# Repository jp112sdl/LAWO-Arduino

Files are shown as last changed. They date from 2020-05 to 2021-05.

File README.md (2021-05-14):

# LAWO-FlipDot
Arduino library for LAWO XY5 flipdot displays (also for GORBA and other FP2800 based flipdot displays)

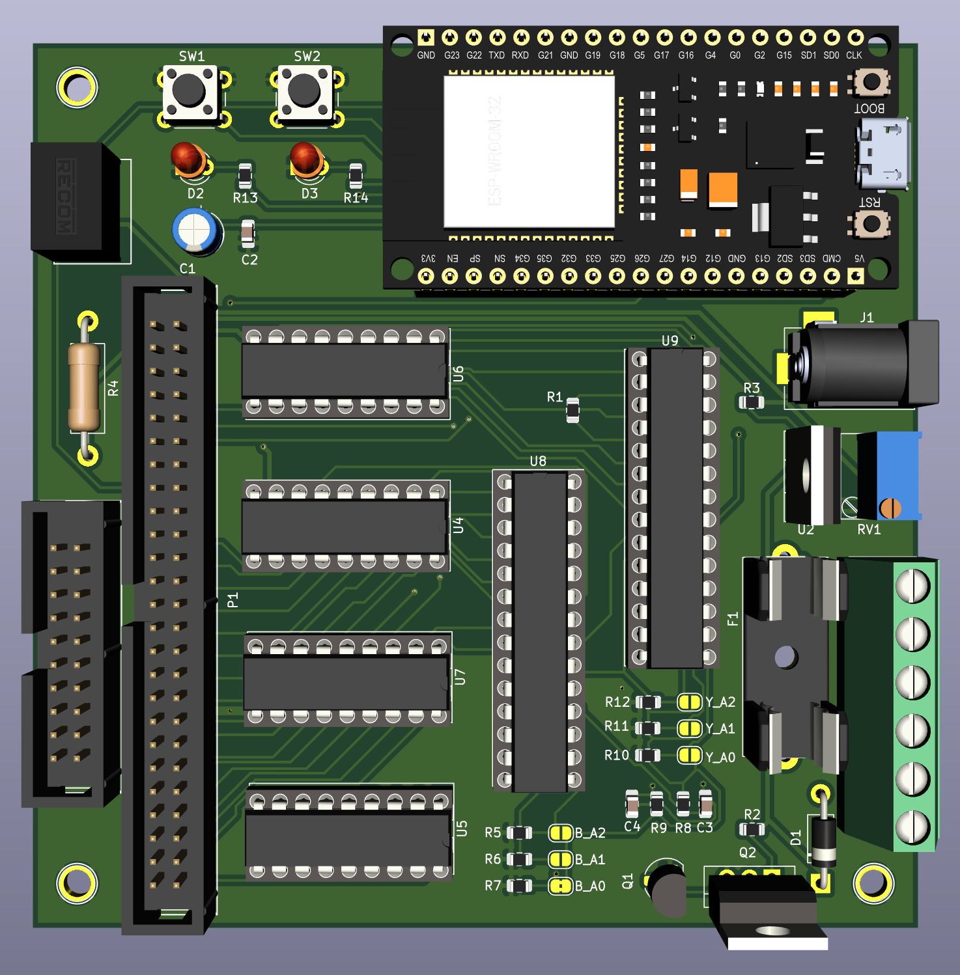
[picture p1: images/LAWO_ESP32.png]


### BOM (mostly from reichelt.de)

| Qty	| Reference(s)	| Value |	Order No. / URL	| Supplier
|---|---|---|---|---|
|1|	C1	|100u	|RAD 100/25|	reichelt
|3 |	C2, C3, C4|100n|	X7R-5 100N	|reichelt
|1|	F1	|T500mA	|RND 170-00041	|reichelt
|1|	F1	|Fuse Holder |RND 170-00188 |reichelt
|1|P1	|MATRIX	|WSL 50G	|reichelt
|1|P2	|MUX|	WSL 20G	|reichelt
|1|Q1	|BC547|	BC 547C	|reichelt
|1|Q2	|IRF740	|IRF 740	|reichelt
|1|	R4|	56|	2W METALL 56	|reichelt
|1|	RV1|	5k|	64W-5,0K|	reichelt
|1	|U1|LC78_05-0.5	|LC78_05-0.5	|reichelt
|1|	U2	|LM317T	|LM 317-220	|reichelt
|1| J1 | Barrel Jack | DC BU25 90|reichelt
|1| J2 | 1x6 Screw Terminal Block, 5mm | RND 205-00049 |reichelt
|1| D1| 1N4001 | 1N 4001|reichelt|
|1| D2| LED1 | LED 3MM GN |reichelt|
|1| D3| LED2 | LED 3MM RT|reichelt
|2| SW1, SW2| TASTER 9303 | reichelt
|4| U4,U5,U6,U7	|Sockel	|GS 18	|reichelt
|2|U8,U9	|Sockel	|GS 28-S	|reichelt
|2| U5,U4	|ULN2803A	|ULN 2803A|	reichelt
|2	|U6,U7	|UDN2981A	|UDN 2981	|reichelt
|2| U8, U9 | MCP23017 | MCP 23017-E/SP | reichelt
|2| R13, R14 | 330 SMD 0805 | RND 0805 1 330 | reichelt
|1| R3 | 240 SMD 0805 | RND 0805 1 240 | reichelt
|2| R17, R18 | 4k7 SMD 0805 | RND 0805 1 4,7K  | reichelt
|12| R1, R2, R5, R6, R7, R8, R9, R10, R11, R12, R15, R16 | 10k SMD 0805 | RND 0805 1 10K  | reichelt
| 1 | U3 | ESP32 Module | AZDelivery ESP32 NodeMCU Module | [amazon.de](https://www.amazon.de/AZDelivery-NodeMCU-Development-Nachfolgermodell-ESP8266/dp/B071P98VTG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)

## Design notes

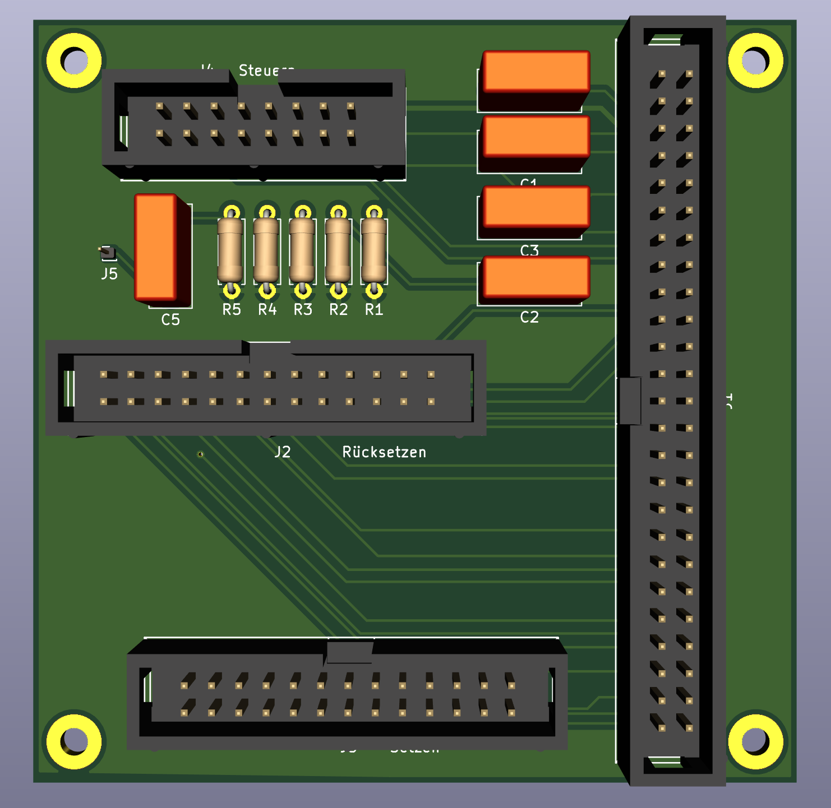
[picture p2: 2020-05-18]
images/GORBA_LAWO_Adapter.png

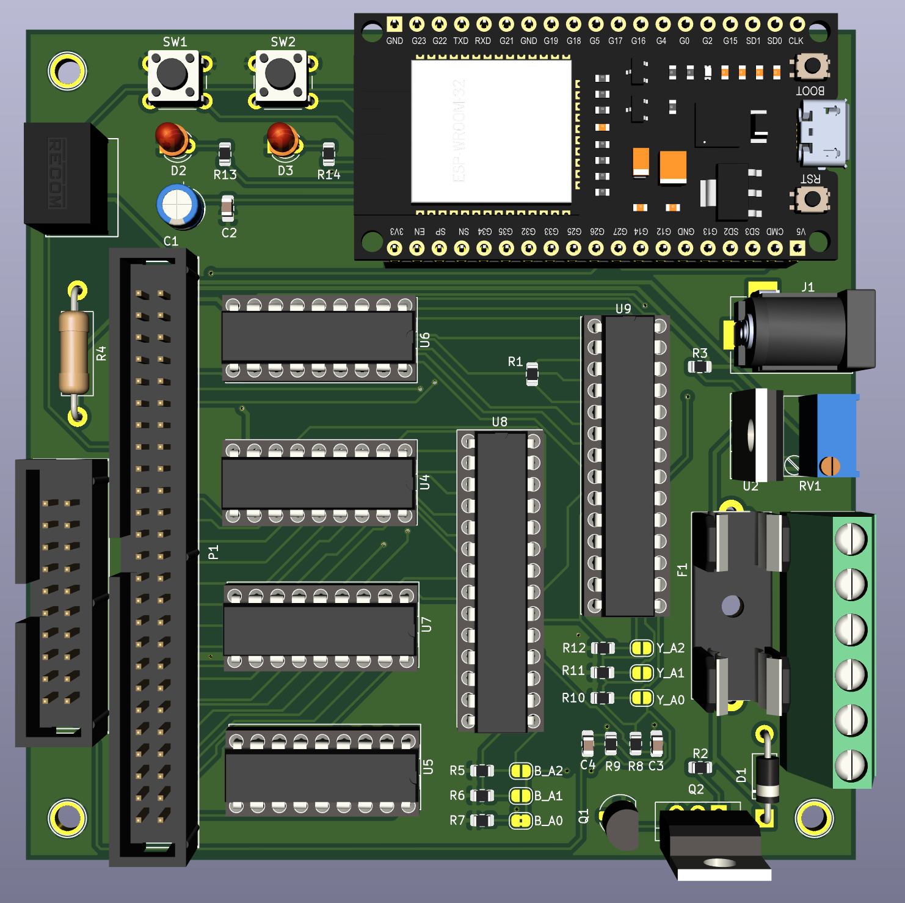
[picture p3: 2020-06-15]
PCB/LAWO_ESP32/LAWO_ESP32.png

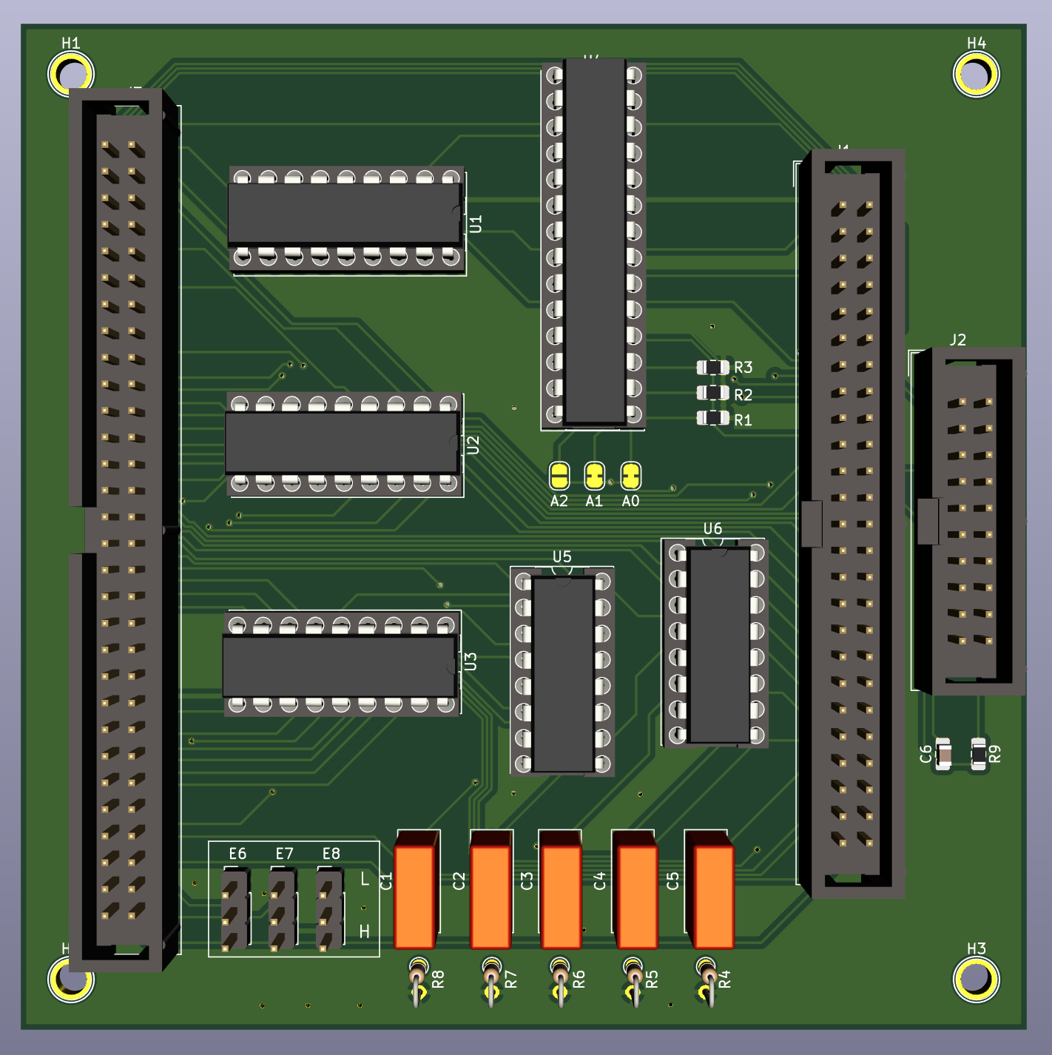
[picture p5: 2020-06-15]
PCB/BROSE_LAWO_Adapter/BROSE_LAWO_Adapter.dsn.png

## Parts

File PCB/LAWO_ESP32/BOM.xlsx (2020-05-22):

Reference | Value | Footprint | Datasheet | Feld4
C1 | 100n | Capacitor_SMD:C_0805_2012Metric_Pad1.15x1.40mm_HandSolder
C2 | 100u | Capacitors_THT:CP_Radial_D5.0mm_P2.00mm
C3 | 100n | Capacitor_SMD:C_0805_2012Metric_Pad1.15x1.40mm_HandSolder | ~
C4 | 100n | Capacitor_SMD:C_0805_2012Metric_Pad1.15x1.40mm_HandSolder | ~
D1 | 1N4001 | Diode_THT:D_DO-41_SOD81_P10.16mm_Horizontal
D2 | LED1 | LED_THT:LED_D3.0mm | ~
D3 | LED2 | LED_THT:LED_D3.0mm | ~
F1 | T500mA | Fuse_Holders_and_Fuses:Fuseholder5x20_horiz_open_Schurter_0031_8201
J1 | Barrel_Jack | Connectors:BARREL_JACK | ~
J2 | Screw_Terminal_01x06 | Connectors_Terminal_Blocks:TerminalBlock_bornier-6_P5.08mm | ~
P1 | MATRIX | Connect:IDC_Header_Straight_50pins
P2 | MUX | Connect:IDC_Header_Straight_20pins
Q1 | BC547 | Package_TO_SOT_THT:TO-92_HandSolder | http://www.fairchildsemi.com/ds/BC/BC547.pdf
Q2 | IRF740 | Package_TO_SOT_THT:TO-220-3_Vertical | http://www.vishay.com/docs/91054/91054.pdf
R1 | 10k | Resistor_SMD:R_0805_2012Metric
R10 | 10k | Resistor_SMD:R_0805_2012Metric | ~
R11 | 10k | Resistor_SMD:R_0805_2012Metric | ~
R12 | 10k | Resistor_SMD:R_0805_2012Metric | ~
R13 | 330 | Resistor_SMD:R_0805_2012Metric | ~
R14 | 330 | Resistor_SMD:R_0805_2012Metric | ~
R15 | 10k | Resistor_SMD:R_0805_2012Metric
R16 | 10k | Resistor_SMD:R_0805_2012Metric
R17 | 4,7k | Resistor_SMD:R_0805_2012Metric | ~
R18 | 4,7k | Resistor_SMD:R_0805_2012Metric | ~
R2 | 10k | Resistor_SMD:R_0805_2012Metric
R3 | 240 | Resistor_SMD:R_0805_2012Metric
R4 | 56 | Resistor_THT:R_Axial_DIN0411_L9.9mm_D3.6mm_P15.24mm_Horizontal
R5 | 10k | Resistor_SMD:R_0805_2012Metric | ~
R6 | 10k | Resistor_SMD:R_0805_2012Metric | ~
R7 | 10k | Resistor_SMD:R_0805_2012Metric | ~
R8 | 10k | Resistor_SMD:R_0805_2012Metric | ~
R9 | 10k | Resistor_SMD:R_0805_2012Metric | ~
RV1 | 5k | Potentiometers:Potentiometer_Trimmer_Bourns_3299W
SW1 | T1 | Buttons_Switches_THT:SW_PUSH_6mm_h5mm | ~
SW2 | T2 | Buttons_Switches_THT:SW_PUSH_6mm_h5mm | ~
U1 | LC78_05-0.5 | Package_SIP:SIP3_11.6x8.5mm | http://www.st.com/content/ccc/resource/technical/document/datasheet/41/4f/b3/b0/12/d4/47/88/CD00000444.pdf/files/CD00000444.pdf/jcr:content/translations/en.CD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
U2 | LM317T | TO_SOT_Packages_THT:TO-220-3_Vertical
U3 | ESP32-DEVKITC-32D | additional:MODULE_ESP32-DEVKITC-32D | Espressif Systems | 4
U4 | ULN2803A | Package_DIP:DIP-18_W7.62mm_Socket
U5 | ULN2803A | Package_DIP:DIP-18_W7.62mm_Socket
U6 | UDN2981A / TBD62783AFG | Package_DIP:DIP-18_W7.62mm_Socket
U7 | UDN2981A / TBD62783AFG | Package_DIP:DIP-18_W7.62mm_Socket
U8 | MCP23017 | Package_DIP:DIP-28_W7.62mm_Socket | http://ww1.microchip.com/downloads/en/DeviceDoc/20001952C.pdf
U9 | MCP23017 | Package_DIP:DIP-28_W7.62mm_Socket | http://ww1.microchip.com/downloads/en/DeviceDoc/20001952C.pdf

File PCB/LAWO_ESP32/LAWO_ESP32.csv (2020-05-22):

Reference | Value | Footprint | Datasheet | Feld4
F1 | T500mA | Fuse_Holders_and_Fuses:Fuseholder5x20_horiz_open_Schurter_0031_8201
R5 | 10k | Resistor_SMD:R_0805_2012Metric | ~
R6 | 10k | Resistor_SMD:R_0805_2012Metric | ~
R1 | 10k | Resistor_SMD:R_0805_2012Metric
R7 | 10k | Resistor_SMD:R_0805_2012Metric | ~
R2 | 10k | Resistor_SMD:R_0805_2012Metric
R8 | 10k | Resistor_SMD:R_0805_2012Metric | ~
R3 | 240 | Resistor_SMD:R_0805_2012Metric
R4 | 56 | Resistor_THT:R_Axial_DIN0411_L9.9mm_D3.6mm_P15.24mm_Horizontal
R9 | 10k | Resistor_SMD:R_0805_2012Metric | ~
R10 | 10k | Resistor_SMD:R_0805_2012Metric | ~
R11 | 10k | Resistor_SMD:R_0805_2012Metric | ~
R12 | 10k | Resistor_SMD:R_0805_2012Metric | ~
JP1 | B_A2 | Jumper:SolderJumper-2_P1.3mm_Open_RoundedPad1.0x1.5mm | ~
JP2 | B_A1 | Jumper:SolderJumper-2_P1.3mm_Open_RoundedPad1.0x1.5mm | ~
JP3 | B_A0 | Jumper:SolderJumper-2_P1.3mm_Bridged2Bar_RoundedPad1.0x1.5mm | ~
JP4 | Y_A0 | Jumper:SolderJumper-2_P1.3mm_Open_RoundedPad1.0x1.5mm | ~
JP5 | Y_A1 | Jumper:SolderJumper-2_P1.3mm_Open_RoundedPad1.0x1.5mm | ~
JP6 | Y_A2 | Jumper:SolderJumper-2_P1.3mm_Open_RoundedPad1.0x1.5mm | ~
D1 | 1N4001 | Diode_THT:D_DO-41_SOD81_P10.16mm_Horizontal
MH1 | MountingHole | Connect:1pin
MH2 | MountingHole | Connect:1pin
MH3 | MountingHole | Connect:1pin
MH4 | MountingHole | Connect:1pin
C3 | 100n | Capacitor_SMD:C_0805_2012Metric_Pad1.15x1.40mm_HandSolder | ~
C2 | 100u | Capacitors_THT:CP_Radial_D5.0mm_P2.00mm
C1 | 100n | Capacitor_SMD:C_0805_2012Metric_Pad1.15x1.40mm_HandSolder
C4 | 100n | Capacitor_SMD:C_0805_2012Metric_Pad1.15x1.40mm_HandSolder | ~
RV1 | 5k | Potentiometers:Potentiometer_Trimmer_Bourns_3299W
J1 | Barrel_Jack | Connectors:BARREL_JACK | ~
U1 | L7805 | Package_SIP:SIP3_11.6x8.5mm | http://www.st.com/content/ccc/resource/technical/document/datasheet/41/4f/b3/b0/12/d4/47/88/CD00000444.pdf/files/CD00000444.pdf/jcr:content/translations/en.CD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
U2 | LM317T | TO_SOT_Packages_THT:TO-220-3_Vertical
P2 | MUX | Connect:IDC_Header_Straight_20pins
P1 | MATRIX | Connect:IDC_Header_Straight_50pins
U4 | ULN2803A | Package_DIP:DIP-18_W7.62mm_Socket
U5 | ULN2803A | Package_DIP:DIP-18_W7.62mm_Socket
U6 | UDN2981A / TBD62783AFG | Package_DIP:DIP-18_W7.62mm_Socket
U8 | MCP23017 | Package_DIP:DIP-28_W7.62mm_Socket | http://ww1.microchip.com/downloads/en/DeviceDoc/20001952C.pdf
U9 | MCP23017 | Package_DIP:DIP-28_W7.62mm_Socket | http://ww1.microchip.com/downloads/en/DeviceDoc/20001952C.pdf
U3 | ESP32-DEVKITC-32D | additional:MODULE_ESP32-DEVKITC-32D | Espressif Systems | 4
J2 | Screw_Terminal_01x06 | Connectors_Terminal_Blocks:TerminalBlock_bornier-6_P5.08mm | ~
U7 | UDN2981A / TBD62783AFG | Package_DIP:DIP-18_W7.62mm_Socket
Q2 | IRF740 | Package_TO_SOT_THT:TO-220-3_Vertical | http://www.vishay.com/docs/91054/91054.pdf
Q1 | BC547 | Package_TO_SOT_THT:TO-92_HandSolder | http://www.fairchildsemi.com/ds/BC/BC547.pdf
SW1 | T1 | Buttons_Switches_THT:SW_PUSH_6mm_h5mm | ~
SW2 | T2 | Buttons_Switches_THT:SW_PUSH_6mm_h5mm | ~
R13 | 330 | Resistor_SMD:R_0805_2012Metric | ~
D2 | LED1 | LED_THT:LED_D3.0mm | ~
R14 | 330 | Resistor_SMD:R_0805_2012Metric | ~
D3 | LED2 | LED_THT:LED_D3.0mm | ~
R15 | 10k | Resistor_SMD:R_0805_2012Metric
R16 | 10k | Resistor_SMD:R_0805_2012Metric
R17 | 4,7k | Resistor_SMD:R_0805_2012Metric | ~
R18 | 4,7k | Resistor_SMD:R_0805_2012Metric | ~

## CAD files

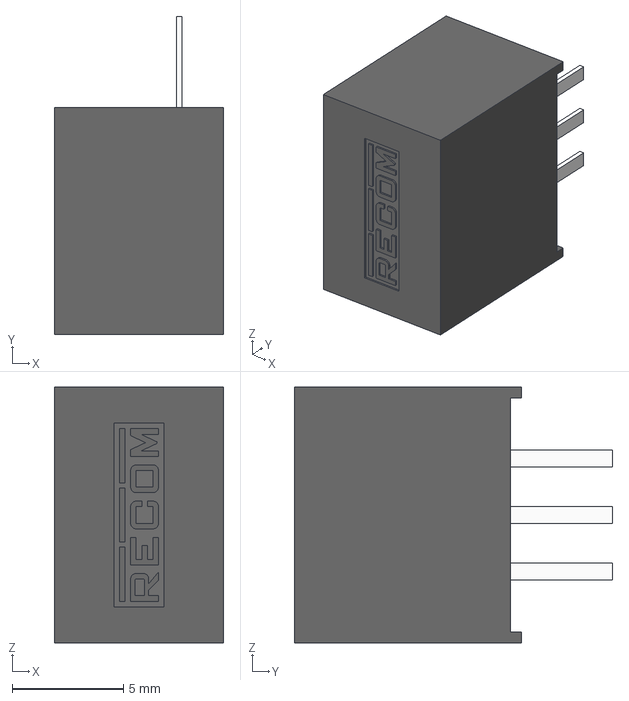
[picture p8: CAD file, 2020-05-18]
PCB/LAWO_ESP32/additional/R-782.5-0.5--3DModel-STEP-1.STEP
7.60 x 14.3 x 11.5 mm

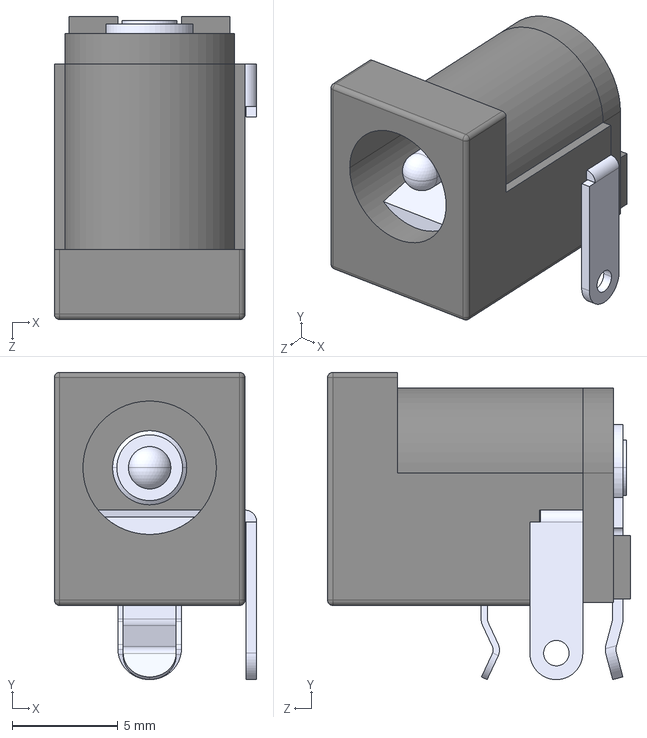
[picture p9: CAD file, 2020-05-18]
PCB/LAWO_ESP32/additional/DCJ200-10-A-K1-K--3DModel-STEP-56544.STEP
9.55 x 14.5 x 14.3 mm

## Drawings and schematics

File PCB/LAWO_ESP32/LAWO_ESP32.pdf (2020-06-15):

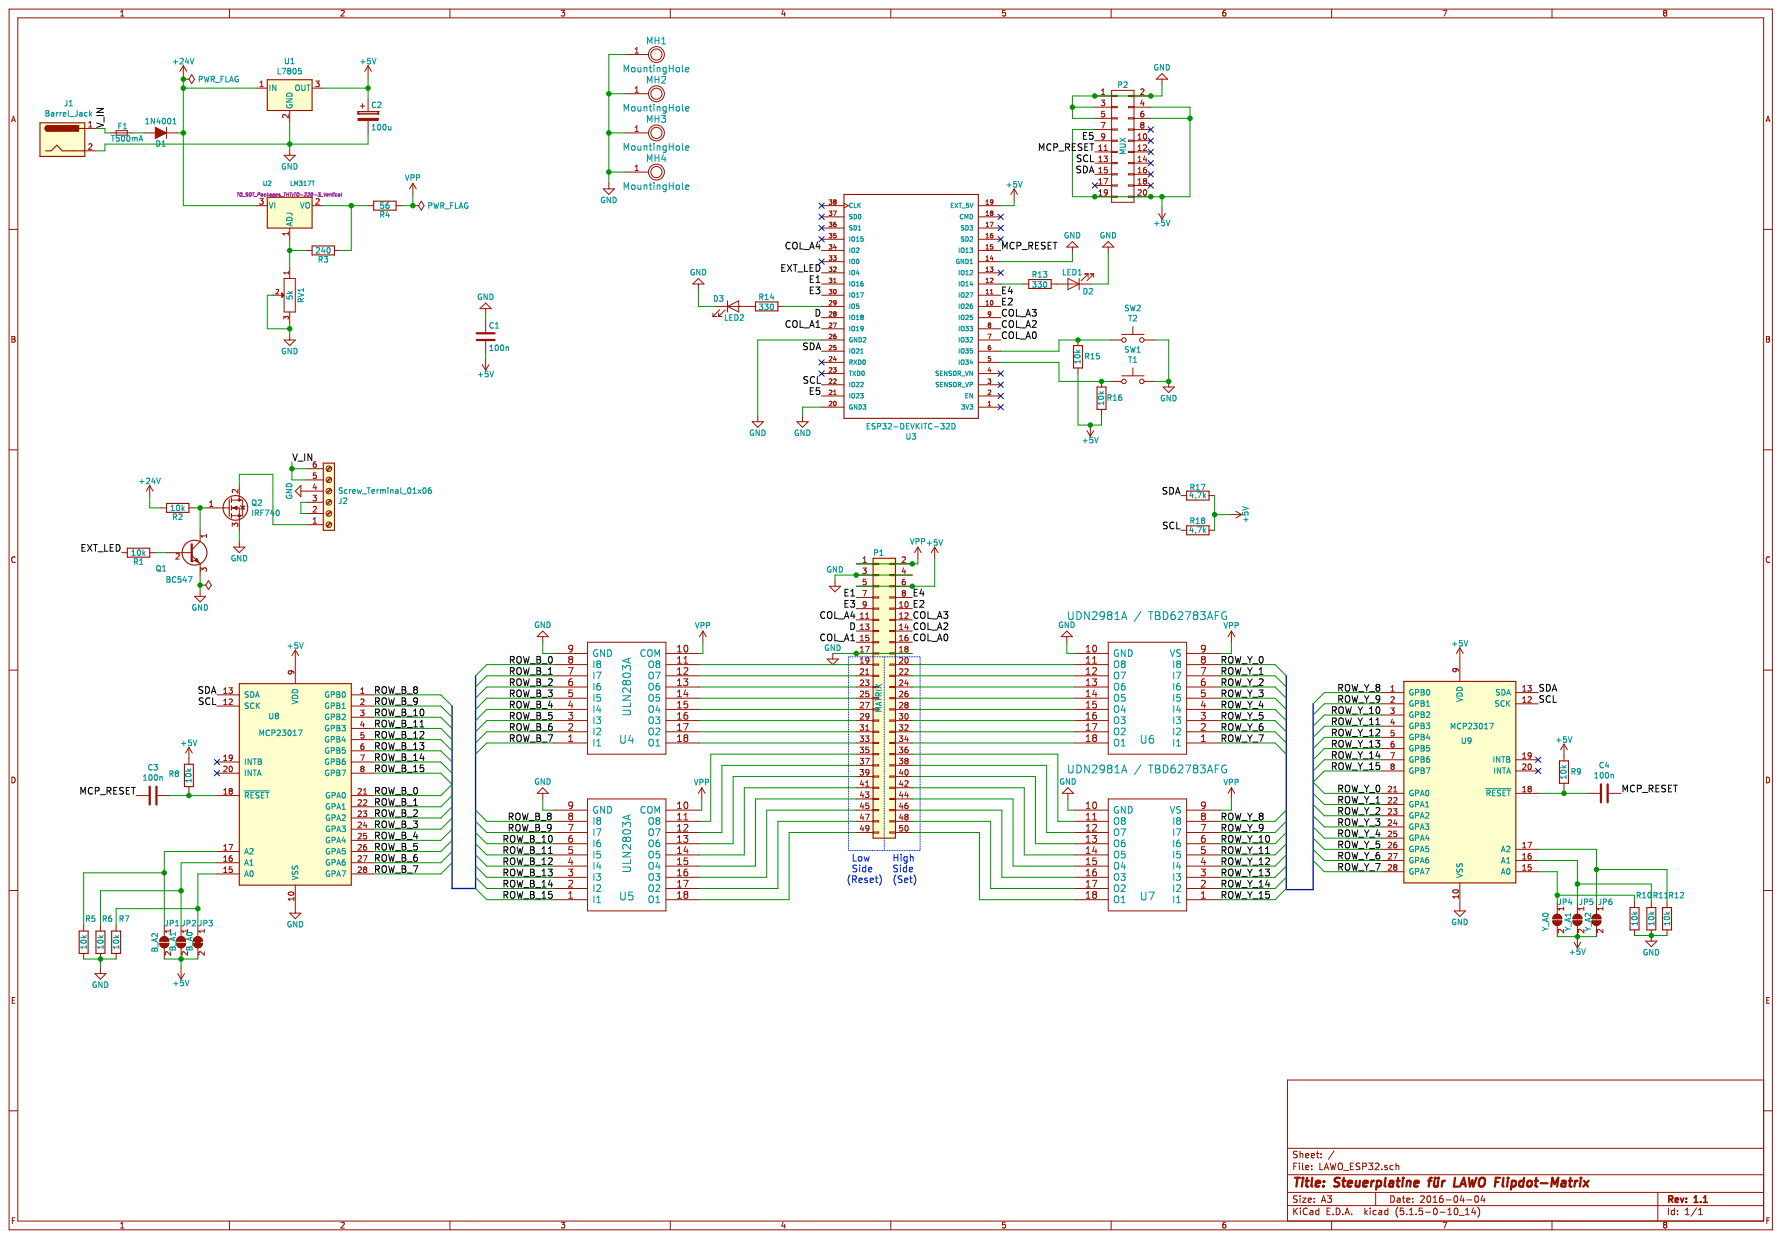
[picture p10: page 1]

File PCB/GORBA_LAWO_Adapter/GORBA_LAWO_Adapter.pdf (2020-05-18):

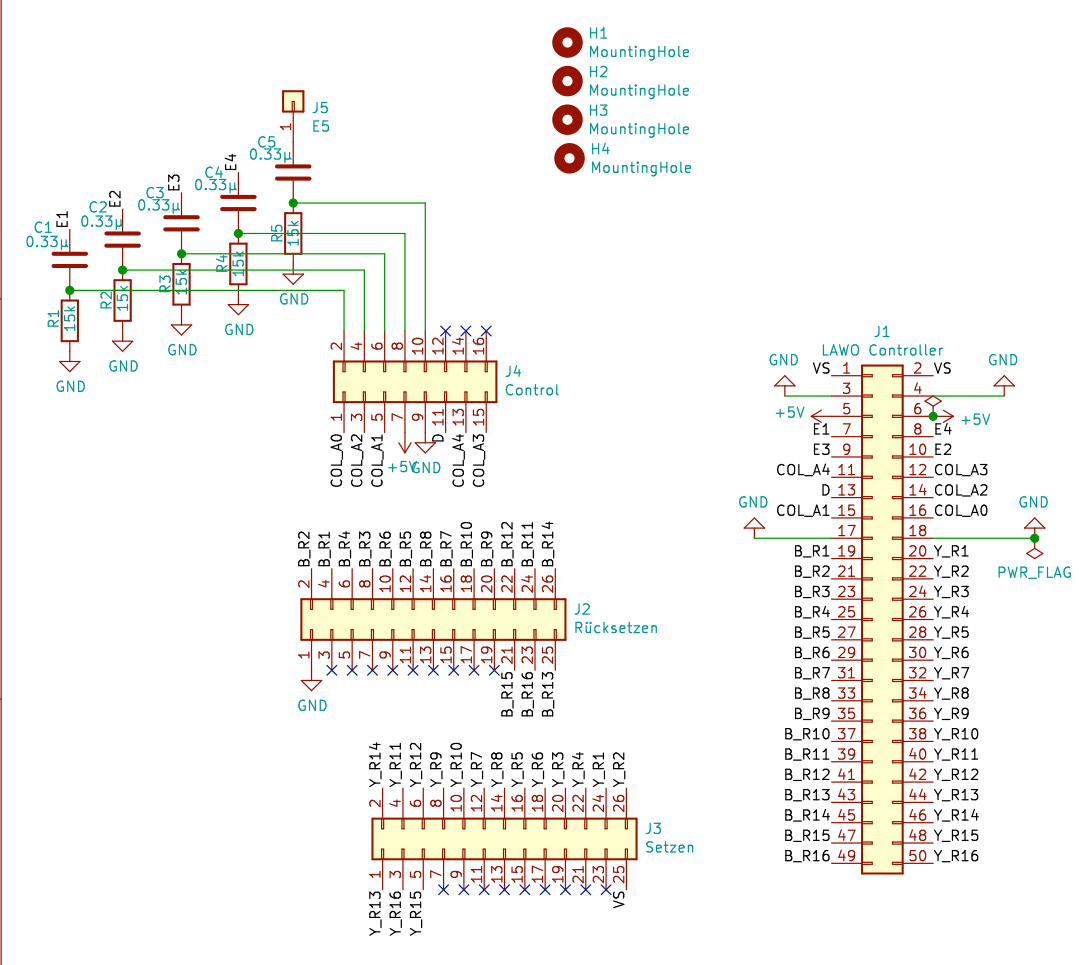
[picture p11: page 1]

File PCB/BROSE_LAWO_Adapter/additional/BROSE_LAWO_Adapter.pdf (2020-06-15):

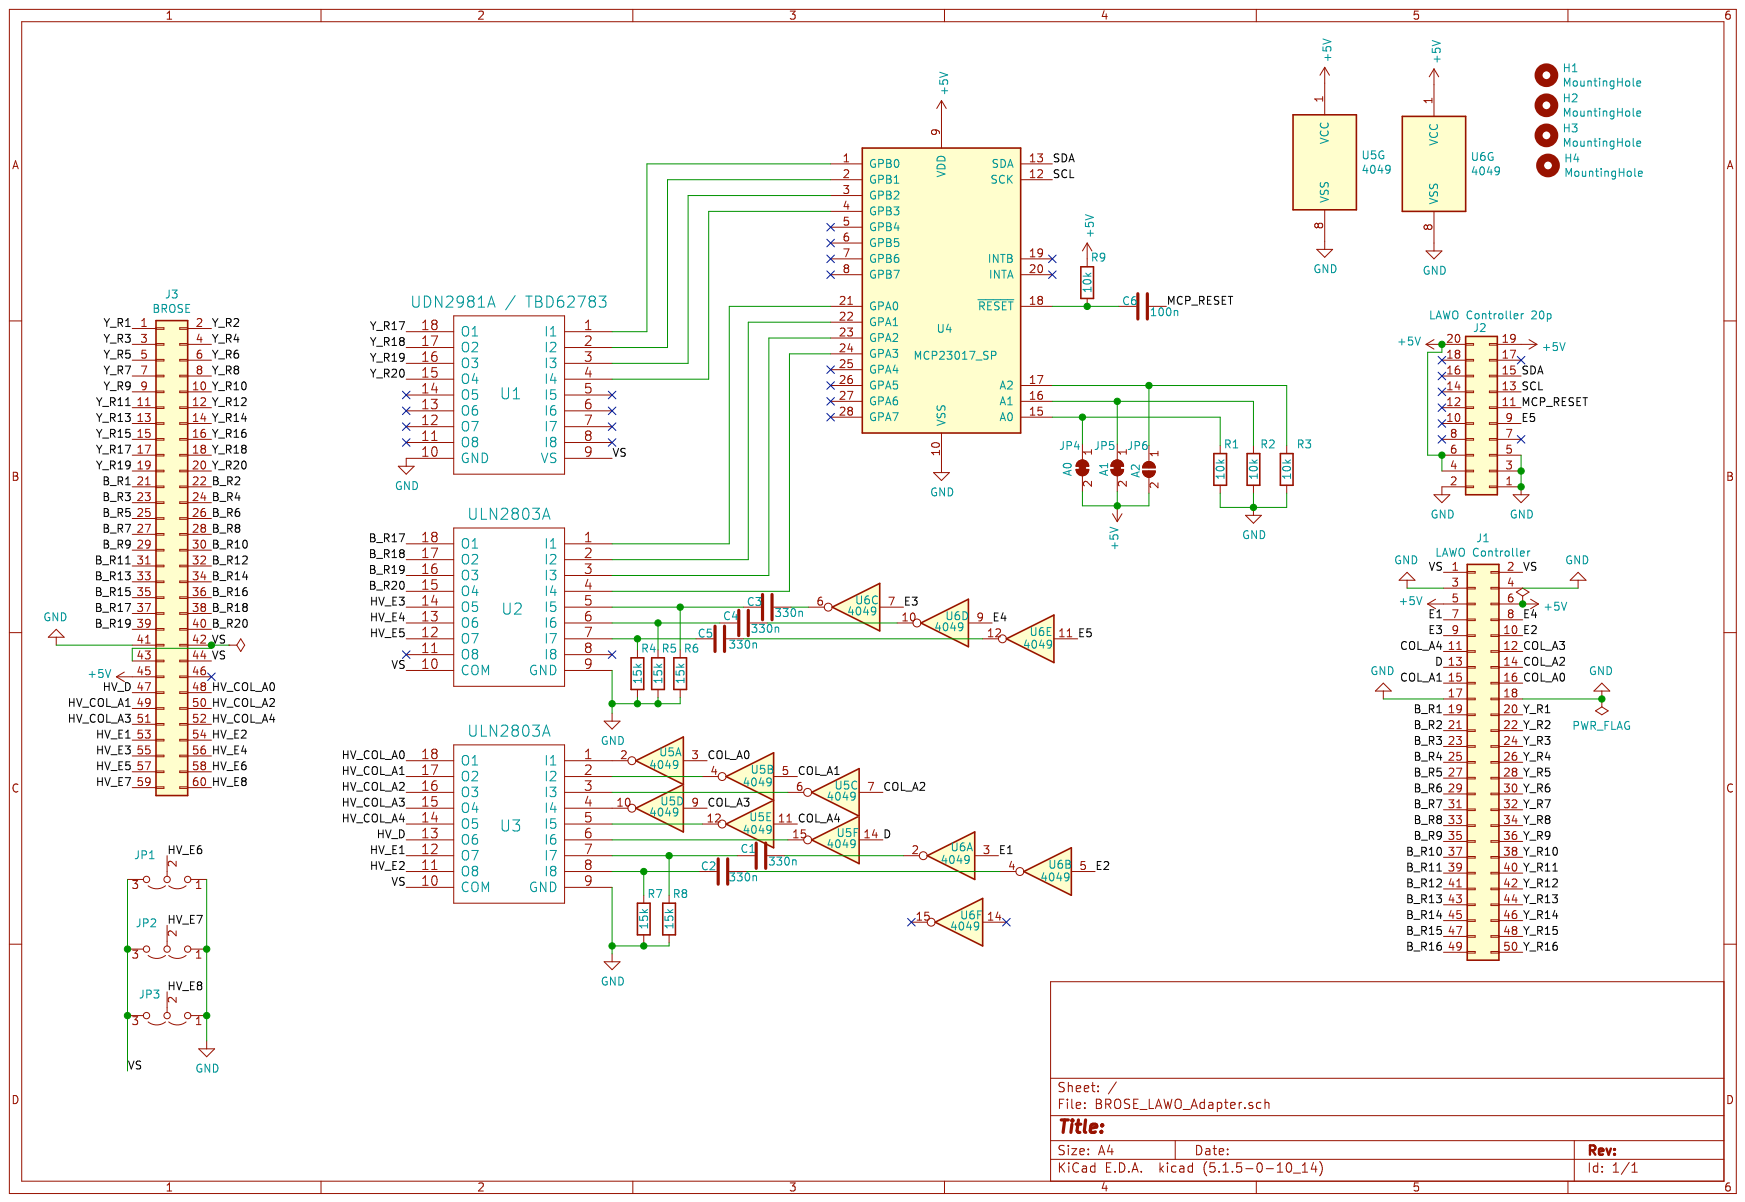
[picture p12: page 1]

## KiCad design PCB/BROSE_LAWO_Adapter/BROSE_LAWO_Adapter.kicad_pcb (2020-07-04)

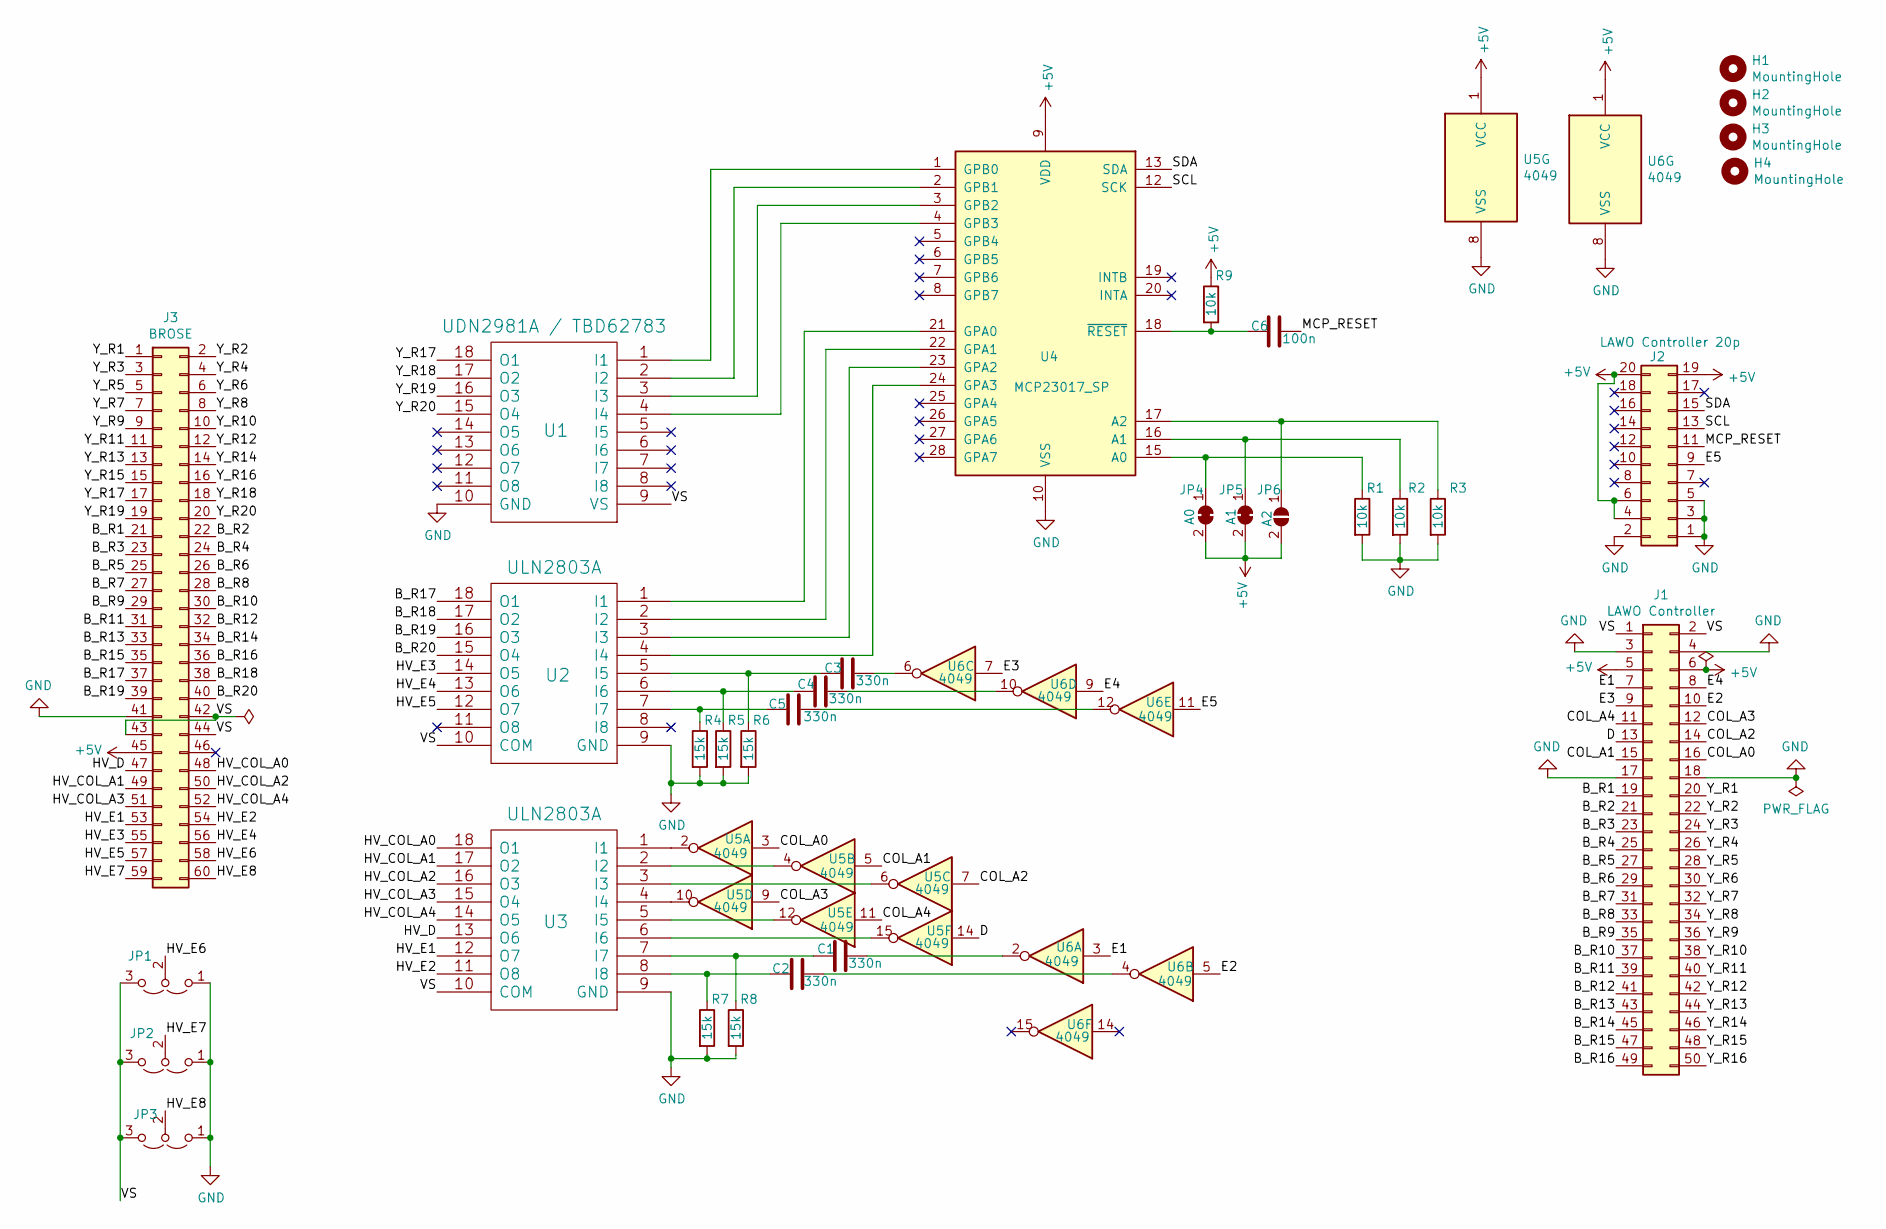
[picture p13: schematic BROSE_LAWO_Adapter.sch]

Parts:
C1, C2, C3, C4, C5: 330n; C_Rect_L10.0mm_W4.0mm_P7.50mm_MKS4
C6: 100n; C_0805_2012Metric_Pad1.15x1.40mm_HandSolder
H1, H2, H3, H4: MountingHole; 1pin
J1: LAWO Controller; IDC-Header_2x25_P2.54mm_Vertical
J2: LAWO Controller 20p; IDC-Header_2x10_P2.54mm_Vertical
J3: BROSE; IDC-Header_2x30_P2.54mm_Vertical
JP1: E6; PinHeader_1x03_P2.54mm_Vertical
JP2: E7; PinHeader_1x03_P2.54mm_Vertical
JP3: E8; PinHeader_1x03_P2.54mm_Vertical
JP4: A0; SolderJumper-2_P1.3mm_Bridged_RoundedPad1.0x1.5mm
JP5: A1; SolderJumper-2_P1.3mm_Bridged_RoundedPad1.0x1.5mm
JP6: A2; SolderJumper-2_P1.3mm_Open_RoundedPad1.0x1.5mm
R1, R2, R3, R9: 10k; R_0805_2012Metric_Pad1.15x1.40mm_HandSolder
R4, R5, R6, R7, R8: 15k; R_Axial_DIN0204_L3.6mm_D1.6mm_P2.54mm_Vertical
U1: UDN2981A / TBD62783; DIP-18_W7.62mm_Socket
U2, U3: ULN2803A; DIP-18_W7.62mm_Socket
U4: MCP23017_SP; DIP-28_W7.62mm_Socket
U5, U6: 4049; DIP-16_W7.62mm_Socket

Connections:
+5V: J1.5, J1.6, J2.4, J2.6, J2.19, J2.20, J3.45, JP4.2 (B), JP5.2 (B), JP6.2 (B), R9.1, U4.9 (VDD), U5.1 (VCC), U6.1 (VCC)
/B_R1: J1.19, J3.21
/B_R2: J1.21, J3.22
/B_R3: J1.23, J3.23
/B_R4: J1.25, J3.24
/B_R5: J1.27, J3.25
/B_R6: J1.29, J3.26
/B_R7: J1.31, J3.27
/B_R8: J1.33, J3.28
/B_R9: J1.35, J3.29
/B_R10: J1.37, J3.30
/B_R11: J1.39, J3.31
/B_R12: J1.41, J3.32
/B_R13: J1.43, J3.33
/B_R14: J1.45, J3.34
/B_R15: J1.47, J3.35
/B_R16: J1.49, J3.36
/B_R17: J3.37, U2.18 (O1)
/B_R18: J3.38, U2.17 (O2)
/B_R19: J3.39, U2.16 (O3)
/B_R20: J3.40, U2.15 (O4)
/COL_A0: J1.16, U5.3
/COL_A1: J1.15, U5.5
/COL_A2: J1.14, U5.7
/COL_A3: J1.12, U5.9
/COL_A4: J1.11, U5.11
/D: J1.13, U5.14
/E1: J1.7, U6.3
/E2: J1.10, U6.5
/E3: J1.9, U6.7
/E4: J1.8, U6.9
/E5: J2.9, U6.11
/HV_COL_A0: J3.48, U3.18 (O1)
/HV_COL_A1: J3.49, U3.17 (O2)
/HV_COL_A2: J3.50, U3.16 (O3)
/HV_COL_A3: J3.51, U3.15 (O4)
/HV_COL_A4: J3.52, U3.14 (O5)
/HV_D: J3.47, U3.13 (O6)
/HV_E1: J3.53, U3.12 (O7)
/HV_E2: J3.54, U3.11 (O8)
/HV_E3: J3.55, U2.14 (O5)
/HV_E4: J3.56, U2.13 (O6)
/HV_E5: J3.57, U2.12 (O7)
/HV_E6: J3.58, JP1.2 (C)
/HV_E7: J3.59, JP2.2 (C)
/HV_E8: J3.60, JP3.2 (C)
/MCP_RESET: C6.2, J2.11
/SCL: J2.13, U4.12 (SCK)
/SDA: J2.15, U4.13 (SDA)
/VS: J1.1, J1.2, J3.42, J3.43, J3.44, JP1.3 (B), JP2.3 (B), JP3.3 (B), U1.9 (VS), U2.10 (COM), U3.10 (COM)
/Y_R1: J1.20, J3.1
/Y_R2: J1.22, J3.2
/Y_R3: J1.24, J3.3
/Y_R4: J1.26, J3.4
/Y_R5: J1.28, J3.5
/Y_R6: J1.30, J3.6
/Y_R7: J1.32, J3.7
/Y_R8: J1.34, J3.8
/Y_R9: J1.36, J3.9
/Y_R10: J1.38, J3.10
/Y_R11: J1.40, J3.11
/Y_R12: J1.42, J3.12
/Y_R13: J1.44, J3.13
/Y_R14: J1.46, J3.14
/Y_R15: J1.48, J3.15
/Y_R16: J1.50, J3.16
/Y_R17: J3.17, U1.18 (O1)
/Y_R18: J3.18, U1.17 (O2)
/Y_R19: J3.19, U1.16 (O3)
/Y_R20: J3.20, U1.15 (O4)
GND: J1.3, J1.4, J1.17, J1.18, J2.1, J2.2, J2.3, J2.5, J3.41, JP1.1 (A), JP2.1 (A), JP3.1 (A), R1.2, R2.2, R3.2, R4.2, R5.2, R6.2, R7.2, R8.2, U1.10 (GND), U2.9 (GND), U3.9 (GND), U4.10 (VSS), U5.8 (VSS), U6.8 (VSS)
unnamed: C1.1, R8.1, U3.7 (I7)
unnamed: C1.2, U6.2
unnamed: C2.1, R7.1, U3.8 (I8)
unnamed: C2.2, U6.4
unnamed: C3.1, R6.1, U2.5 (I5)
unnamed: C3.2, U6.6
unnamed: C4.1, R5.1, U2.6 (I6)
unnamed: C4.2, U6.10
unnamed: C5.1, R4.1, U2.7 (I7)
unnamed: C5.2, U6.12
unnamed: C6.1, R9.2, U4.18 (~RESET~)
unnamed: JP4.1 (A), R1.1, U4.15 (A0)
unnamed: JP5.1 (A), R2.1, U4.16 (A1)
unnamed: JP6.1 (A), R3.1, U4.17 (A2)
unnamed: U1.1 (I1), U4.1 (GPB0)
unnamed: U1.2 (I2), U4.2 (GPB1)
unnamed: U1.3 (I3), U4.3 (GPB2)
unnamed: U1.4 (I4), U4.4 (GPB3)
unnamed: U2.1 (I1), U4.21 (GPA0)
unnamed: U2.2 (I2), U4.22 (GPA1)
unnamed: U2.3 (I3), U4.23 (GPA2)
unnamed: U2.4 (I4), U4.24 (GPA3)
unnamed: U3.1 (I1), U5.2
unnamed: U3.2 (I2), U5.4
unnamed: U3.3 (I3), U5.6
unnamed: U3.4 (I4), U5.10
unnamed: U3.5 (I5), U5.12
unnamed: U3.6 (I6), U5.15

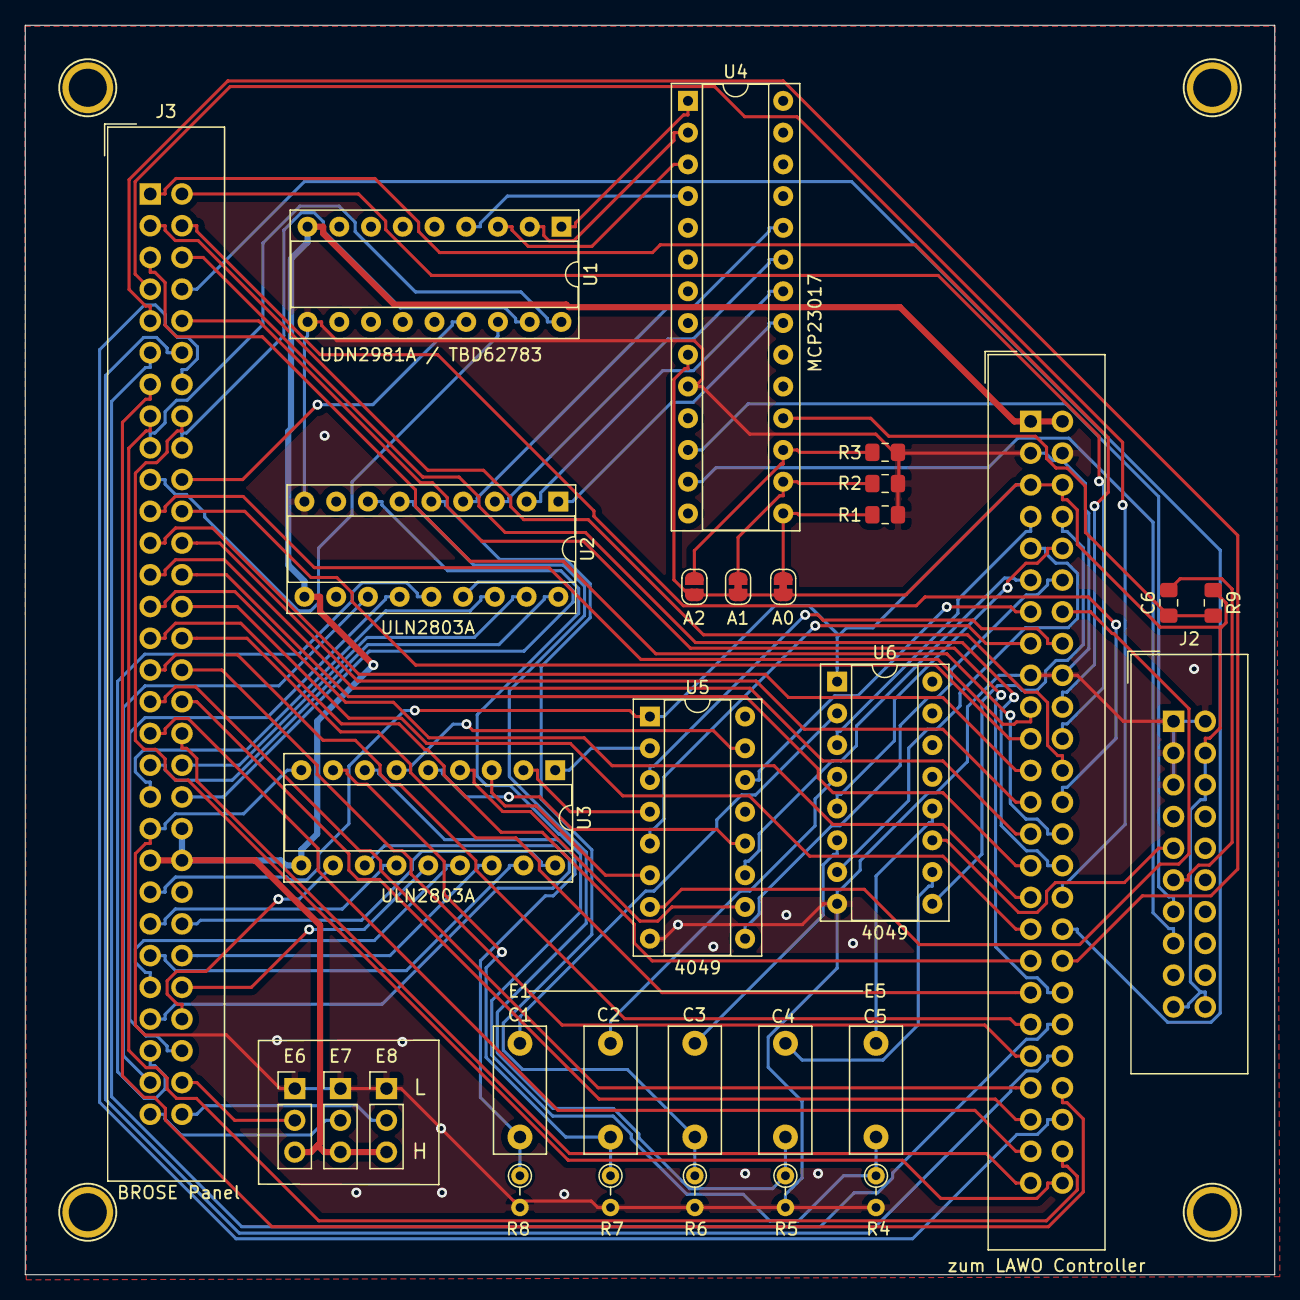
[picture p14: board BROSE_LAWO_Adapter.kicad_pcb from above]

Board: 2 copper layers, 100.0 x 100.0 mm, 34 parts (0 on the bottom side), 99 nets.

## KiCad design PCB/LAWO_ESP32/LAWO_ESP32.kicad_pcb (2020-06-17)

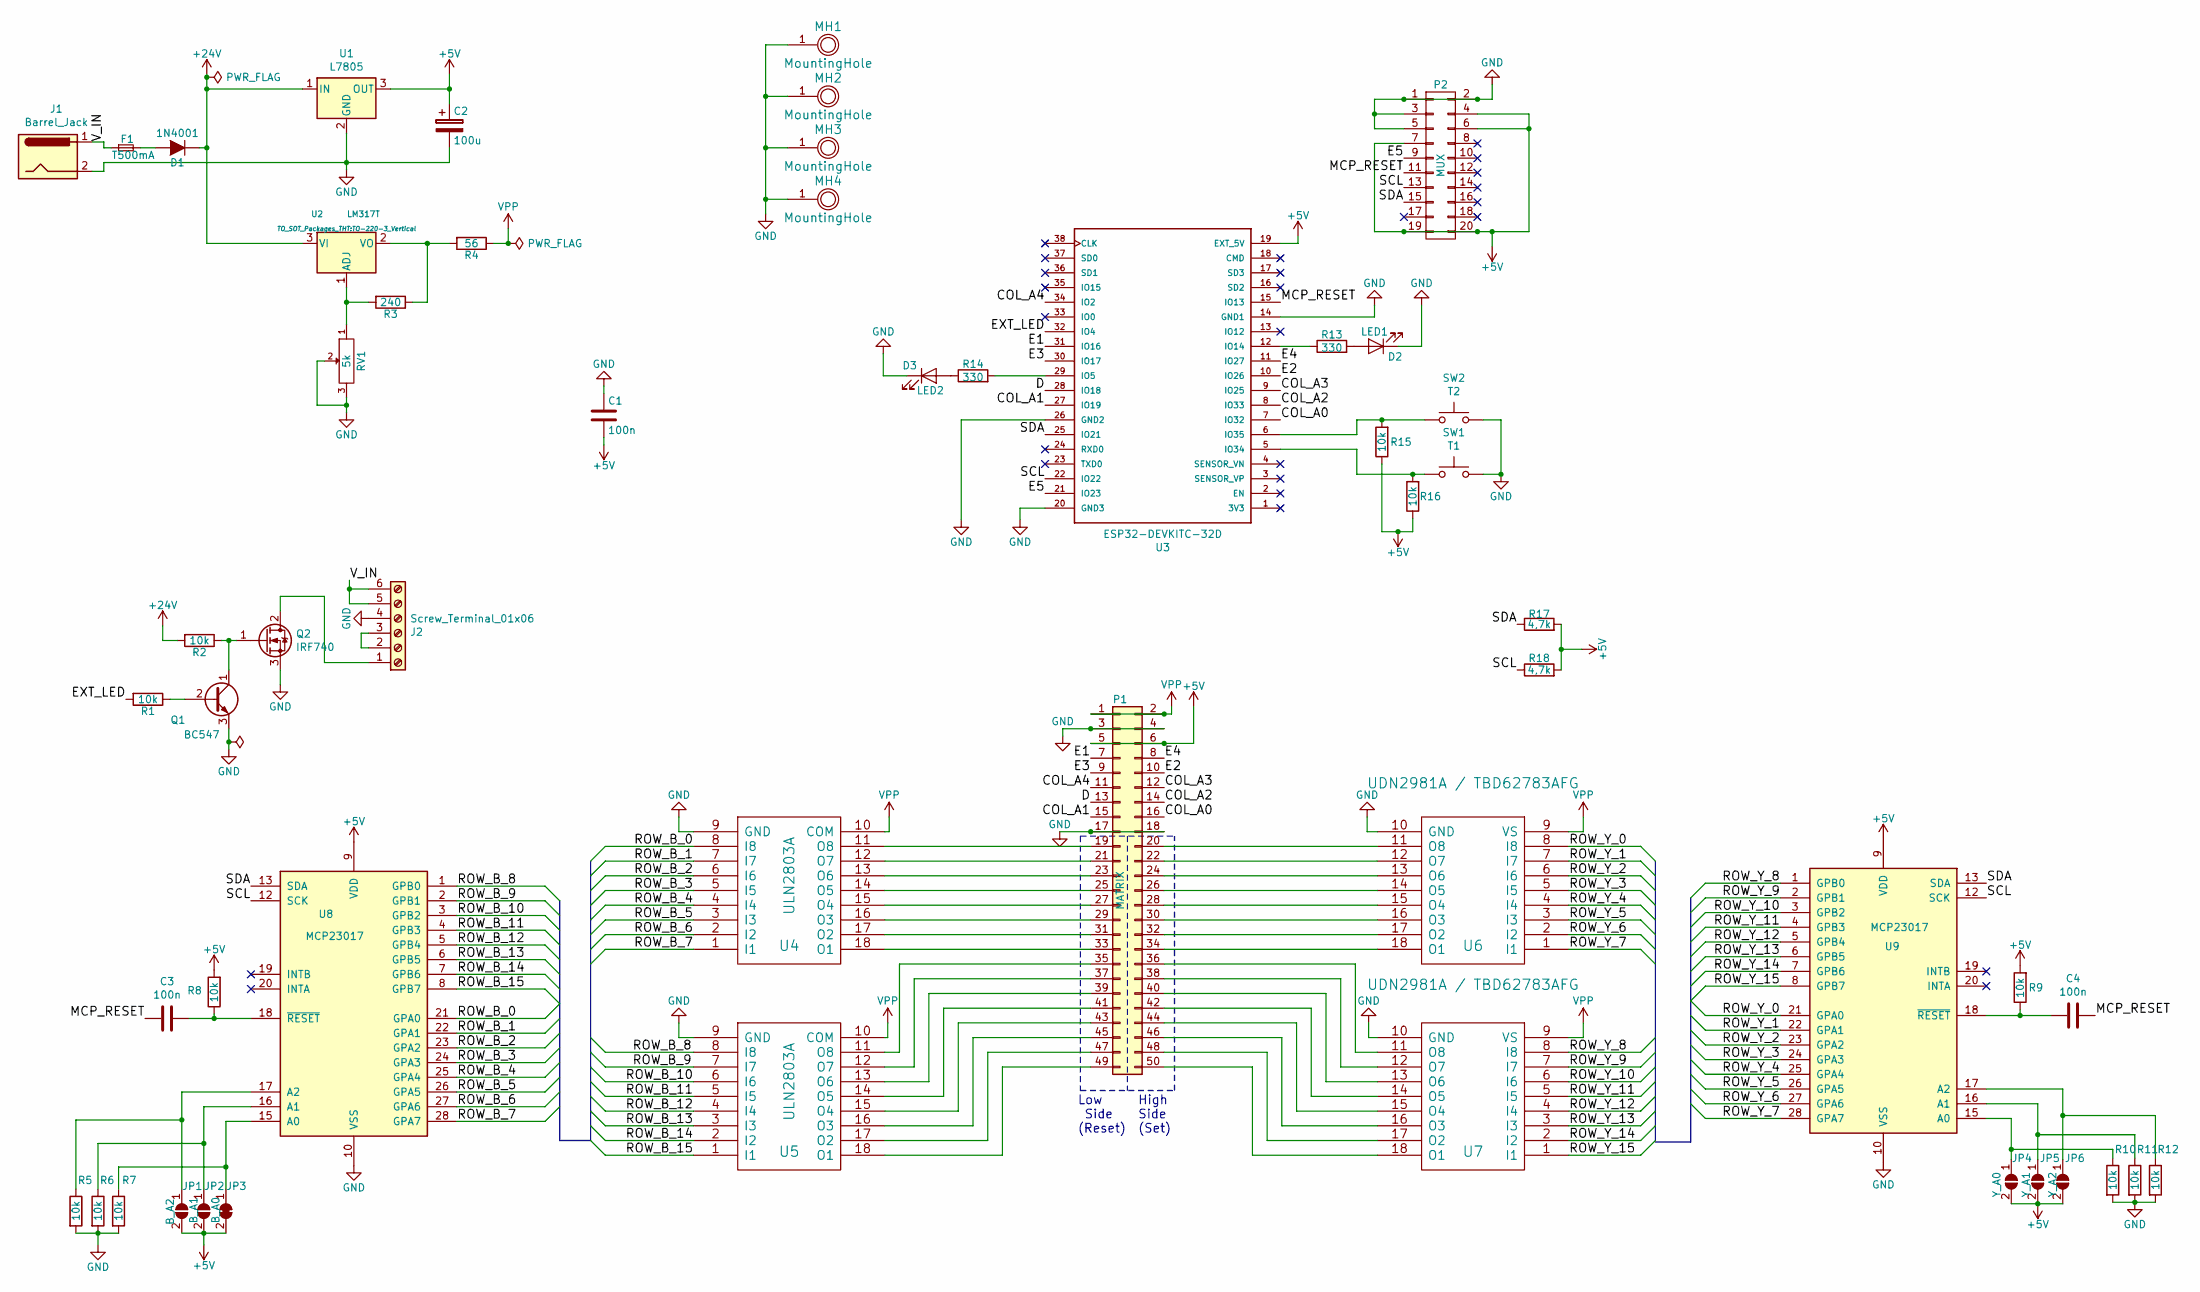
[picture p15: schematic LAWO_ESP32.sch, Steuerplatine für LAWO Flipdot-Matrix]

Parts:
C1, C3, C4: 100n; C_0805_2012Metric_Pad1.15x1.40mm_HandSolder
C2: 100u; CP_Radial_D5.0mm_P2.00mm
D1: 1N4001; D_DO-41_SOD81_P10.16mm_Horizontal
D2: LED1; LED_D3.0mm
D3: LED2; LED_D3.0mm
F1: T500mA; Fuseholder5x20_horiz_open_Schurter_0031_8201
J1: Barrel_Jack; BARREL_JACK
J2: Screw_Terminal_01x06; TerminalBlock_bornier-6_P5.08mm
JP1: B_A2; SolderJumper-2_P1.3mm_Open_RoundedPad1.0x1.5mm
JP2: B_A1; SolderJumper-2_P1.3mm_Open_RoundedPad1.0x1.5mm
JP3: B_A0; SolderJumper-2_P1.3mm_Bridged2Bar_RoundedPad1.0x1.5mm
JP4: Y_A0; SolderJumper-2_P1.3mm_Open_RoundedPad1.0x1.5mm
JP5: Y_A1; SolderJumper-2_P1.3mm_Open_RoundedPad1.0x1.5mm
JP6: Y_A2; SolderJumper-2_P1.3mm_Open_RoundedPad1.0x1.5mm
MH1, MH2, MH3, MH4: MountingHole; 1pin
P1: MATRIX; IDC_Header_Straight_50pins
P2: MUX; IDC_Header_Straight_20pins
Q1: BC547; TO-92_HandSolder
Q2: IRF740; TO-220-3_Vertical
R1, R2, R5, R6, R7, R8, R9, R10, R11, R12, R15, R16: 10k; R_0805_2012Metric
R3: 240; R_0805_2012Metric
R4: 56; R_Axial_DIN0411_L9.9mm_D3.6mm_P15.24mm_Horizontal
R13, R14: 330; R_0805_2012Metric
R17, R18: 4,7k; R_0805_2012Metric
RV1: 5k; Potentiometer_Trimmer_Bourns_3299W
SW1: T1; SW_PUSH_6mm_h5mm
SW2: T2; SW_PUSH_6mm_h5mm
U1: L7805; SIP3_11.6x8.5mm
U2: LM317T; TO-220-3_Vertical
U3: ESP32-DEVKITC-32D; MODULE_ESP32-DEVKITC-32D
U4, U5: ULN2803A; DIP-18_W7.62mm_Socket
U6, U7: UDN2981A / TBD62783AFG; DIP-18_W7.62mm_Socket
U8, U9: MCP23017; DIP-28_W7.62mm_Socket

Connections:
+5V: C1.2, C2.1, JP1.2 (B), JP2.2 (B), JP3.2 (B), JP4.2 (B), JP5.2 (B), JP6.2 (B), P1.5, P1.6, P2.4, P2.6, P2.7, P2.19, P2.20, R8.2, R9.2, R15.1, R16.1, R17.2, R18.2, U1.3 (OUT), U3.19 (EXT_5V), U8.9 (VDD), U9.9 (VDD)
+24V: D1.1 (K), R2.2, U1.1 (IN), U2.3 (VI)
/COL_A0: P1.16, U3.7 (IO32)
/COL_A1: P1.15, U3.27 (IO19)
/COL_A2: P1.14, U3.8 (IO33)
/COL_A3: P1.12, U3.9 (IO25)
/COL_A4: P1.11, U3.34 (IO2)
/D: P1.13, U3.28 (IO18)
/E1: P1.7, U3.31 (IO16)
/E2: P1.10, U3.10 (IO26)
/E3: P1.9, U3.30 (IO17)
/E4: P1.8, U3.11 (IO27)
/E5: P2.9, U3.21 (IO23)
/EXT_LED: R1.2, U3.32 (IO4)
/MCP_RESET: C3.2, C4.1, P2.11, U3.15 (IO13)
/ROW_B_0: U4.8 (I8), U8.21 (GPA0)
/ROW_B_1: U4.7 (I7), U8.22 (GPA1)
/ROW_B_2: U4.6 (I6), U8.23 (GPA2)
/ROW_B_3: U4.5 (I5), U8.24 (GPA3)
/ROW_B_4: U4.4 (I4), U8.25 (GPA4)
/ROW_B_5: U4.3 (I3), U8.26 (GPA5)
/ROW_B_6: U4.2 (I2), U8.27 (GPA6)
/ROW_B_7: U4.1 (I1), U8.28 (GPA7)
/ROW_B_8: U5.8 (I8), U8.1 (GPB0)
/ROW_B_9: U5.7 (I7), U8.2 (GPB1)
/ROW_B_10: U5.6 (I6), U8.3 (GPB2)
/ROW_B_11: U5.5 (I5), U8.4 (GPB3)
/ROW_B_12: U5.4 (I4), U8.5 (GPB4)
/ROW_B_13: U5.3 (I3), U8.6 (GPB5)
/ROW_B_14: U5.2 (I2), U8.7 (GPB6)
/ROW_B_15: U5.1 (I1), U8.8 (GPB7)
/ROW_Y_0: U6.8 (I8), U9.21 (GPA0)
/ROW_Y_1: U6.7 (I7), U9.22 (GPA1)
/ROW_Y_2: U6.6 (I6), U9.23 (GPA2)
/ROW_Y_3: U6.5 (I5), U9.24 (GPA3)
/ROW_Y_4: U6.4 (I4), U9.25 (GPA4)
/ROW_Y_5: U6.3 (I3), U9.26 (GPA5)
/ROW_Y_6: U6.2 (I2), U9.27 (GPA6)
/ROW_Y_7: U6.1 (I1), U9.28 (GPA7)
/ROW_Y_8: U7.8 (I8), U9.1 (GPB0)
/ROW_Y_9: U7.7 (I7), U9.2 (GPB1)
/ROW_Y_10: U7.6 (I6), U9.3 (GPB2)
/ROW_Y_11: U7.5 (I5), U9.4 (GPB3)
/ROW_Y_12: U7.4 (I4), U9.5 (GPB4)
/ROW_Y_13: U7.3 (I3), U9.6 (GPB5)
/ROW_Y_14: U7.2 (I2), U9.7 (GPB6)
/ROW_Y_15: U7.1 (I1), U9.8 (GPB7)
/SCL: P2.13, R18.1, U3.22 (IO22), U8.12 (SCK), U9.12 (SCK)
/SDA: P2.15, R17.1, U3.25 (IO21), U8.13 (SDA), U9.13 (SDA)
/V_IN: F1.1, J1.1, J2.5, J2.6
GND: C1.1, C2.2, D2.1 (K), D3.1 (K), J1.2, J2.4, MH1.1, MH2.1, MH3.1, MH4.1, P1.3, P1.4, P1.17, P1.18, P2.1, P2.2, P2.3, P2.5, Q1.3 (E), Q2.3 (S), R5.2, R6.2, R7.2, R10.2, R11.2, R12.2, RV1.2, RV1.3, SW1.2, SW2.2, U1.2 (GND), U3.14 (GND1), U3.20 (GND3), U3.26 (GND2), U4.9 (GND), U5.9 (GND), U6.10 (GND), U7.10 (GND), U8.10 (VSS), U9.10 (VSS)
unnamed: C3.1, R8.1, U8.18 (~RESET~)
unnamed: C4.2, R9.1, U9.18 (~RESET~)
unnamed: D1.2 (A), F1.2
unnamed: D2.2 (A), R13.2
unnamed: D3.2 (A), R14.1
unnamed: J2.1, Q2.2 (D)
unnamed: J2.2, J2.3
unnamed: JP1.1 (A), R5.1, U8.17 (A2)
unnamed: JP2.1 (A), R6.1, U8.16 (A1)
unnamed: JP3.1 (A), R7.1, U8.15 (A0)
unnamed: JP4.1 (A), R10.1, U9.15 (A0)
unnamed: JP5.1 (A), R11.1, U9.16 (A1)
unnamed: JP6.1 (A), R12.1, U9.17 (A2)
unnamed: P1.19, U4.11 (O8)
unnamed: P1.20, U6.11 (O8)
unnamed: P1.21, U4.12 (O7)
unnamed: P1.22, U6.12 (O7)
unnamed: P1.23, U4.13 (O6)
unnamed: P1.24, U6.13 (O6)
unnamed: P1.25, U4.14 (O5)
unnamed: P1.26, U6.14 (O5)
unnamed: P1.27, U4.15 (O4)
unnamed: P1.28, U6.15 (O4)
unnamed: P1.29, U4.16 (O3)
unnamed: P1.30, U6.16 (O3)
unnamed: P1.31, U4.17 (O2)
unnamed: P1.32, U6.17 (O2)
unnamed: P1.33, U4.18 (O1)
unnamed: P1.34, U6.18 (O1)
unnamed: P1.35, U5.11 (O8)
unnamed: P1.36, U7.11 (O8)
unnamed: P1.37, U5.12 (O7)
unnamed: P1.38, U7.12 (O7)
unnamed: P1.39, U5.13 (O6)
unnamed: P1.40, U7.13 (O6)
unnamed: P1.41, U5.14 (O5)
unnamed: P1.42, U7.14 (O5)
unnamed: P1.43, U5.15 (O4)
unnamed: P1.44, U7.15 (O4)
unnamed: P1.45, U5.16 (O3)
unnamed: P1.46, U7.16 (O3)
unnamed: P1.47, U5.17 (O2)
unnamed: P1.48, U7.17 (O2)
unnamed: P1.49, U5.18 (O1)
unnamed: P1.50, U7.18 (O1)
unnamed: Q1.1 (C), Q2.1 (G), R2.1
unnamed: Q1.2 (B), R1.1
unnamed: R3.1, R4.2, U2.2 (VO)
unnamed: R3.2, RV1.1, U2.1 (ADJ)
unnamed: R13.1, U3.12 (IO14)
unnamed: R14.2, U3.29 (IO5)
unnamed: R15.2, SW2.1, U3.6 (IO35)
unnamed: R16.2, SW1.1, U3.5 (IO34)
VPP: P1.1, P1.2, R4.1, U4.10 (COM), U5.10 (COM), U6.9 (VS), U7.9 (VS)

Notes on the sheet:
Low Side (Reset)
High Side (Set)

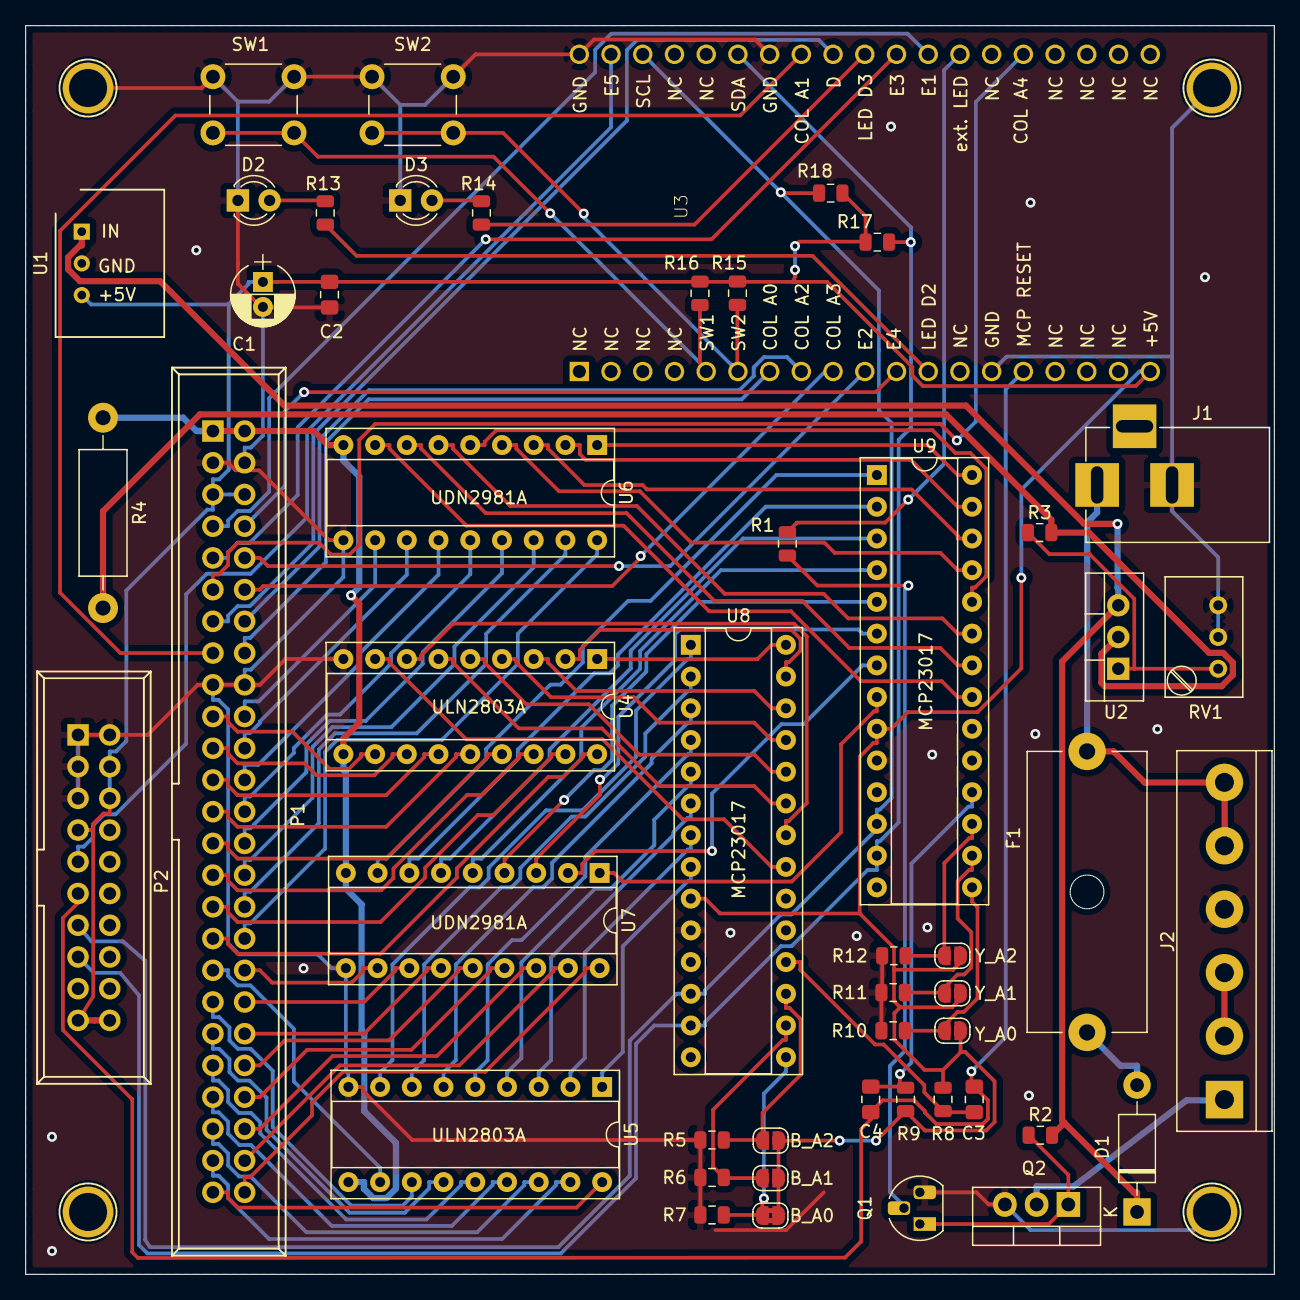
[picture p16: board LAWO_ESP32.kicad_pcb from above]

Board: 2 copper layers, 100.0 x 100.0 mm, 54 parts (0 on the bottom side), 105 nets.

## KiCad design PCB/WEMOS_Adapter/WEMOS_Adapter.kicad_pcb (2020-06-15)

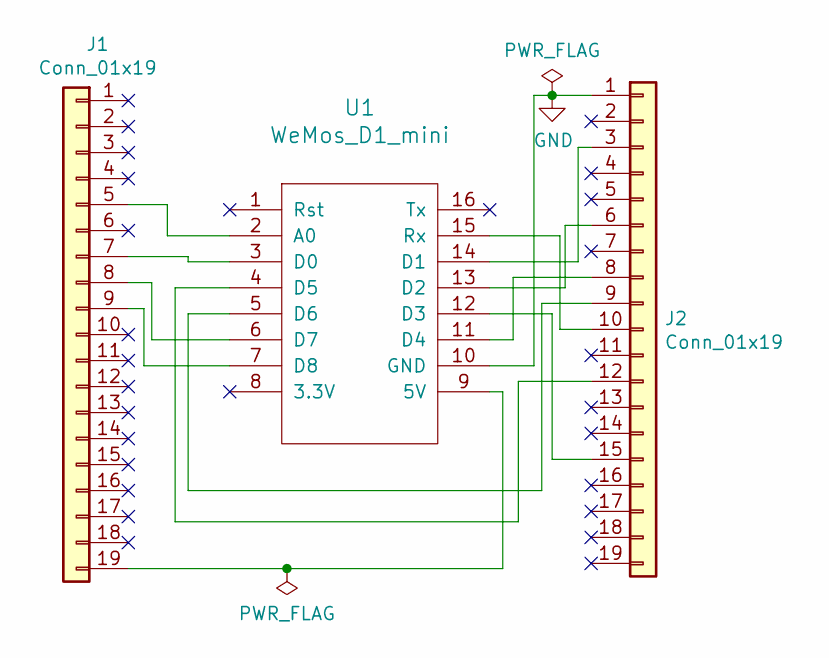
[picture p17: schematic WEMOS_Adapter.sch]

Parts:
J1, J2: Conn_01x19; PinHeader_1x19_P2.54mm_Vertical
U1: WeMos_D1_mini; wemos-d1-mini-connectors-only

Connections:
GND: J2.1, U1.10 (GND)
unnamed: J1.5, U1.2 (A0)
unnamed: J1.7, U1.3 (D0)
unnamed: J1.8, U1.6 (D7)
unnamed: J1.9, U1.7 (D8)
unnamed: J1.19, U1.9 (5V)
unnamed: J2.3, U1.14 (D1)
unnamed: J2.6, U1.13 (D2)
unnamed: J2.8, U1.11 (D4)
unnamed: J2.9, U1.5 (D6)
unnamed: J2.10, U1.15 (Rx)
unnamed: J2.12, U1.4 (D5)
unnamed: J2.15, U1.12 (D3)

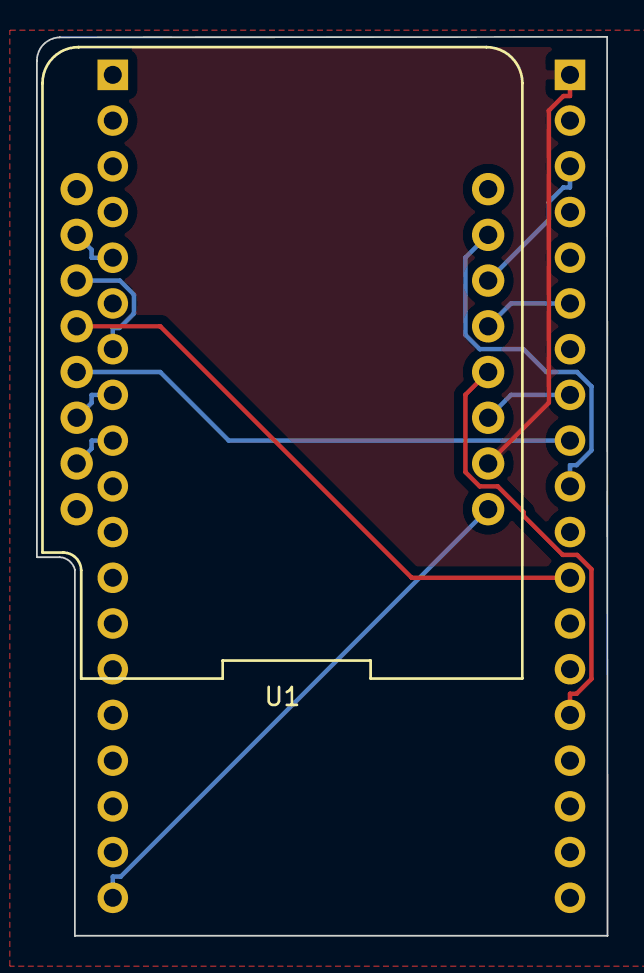
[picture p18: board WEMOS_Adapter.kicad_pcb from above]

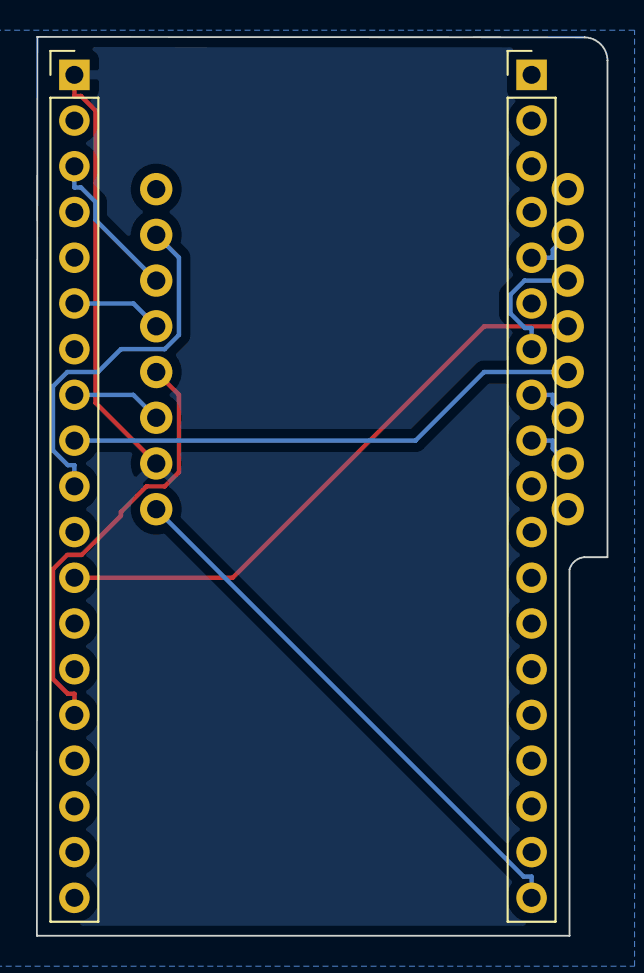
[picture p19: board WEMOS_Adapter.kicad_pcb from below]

Board: 2 copper layers, 31.7 x 49.9 mm, 3 parts (2 on the bottom side), 13 nets.

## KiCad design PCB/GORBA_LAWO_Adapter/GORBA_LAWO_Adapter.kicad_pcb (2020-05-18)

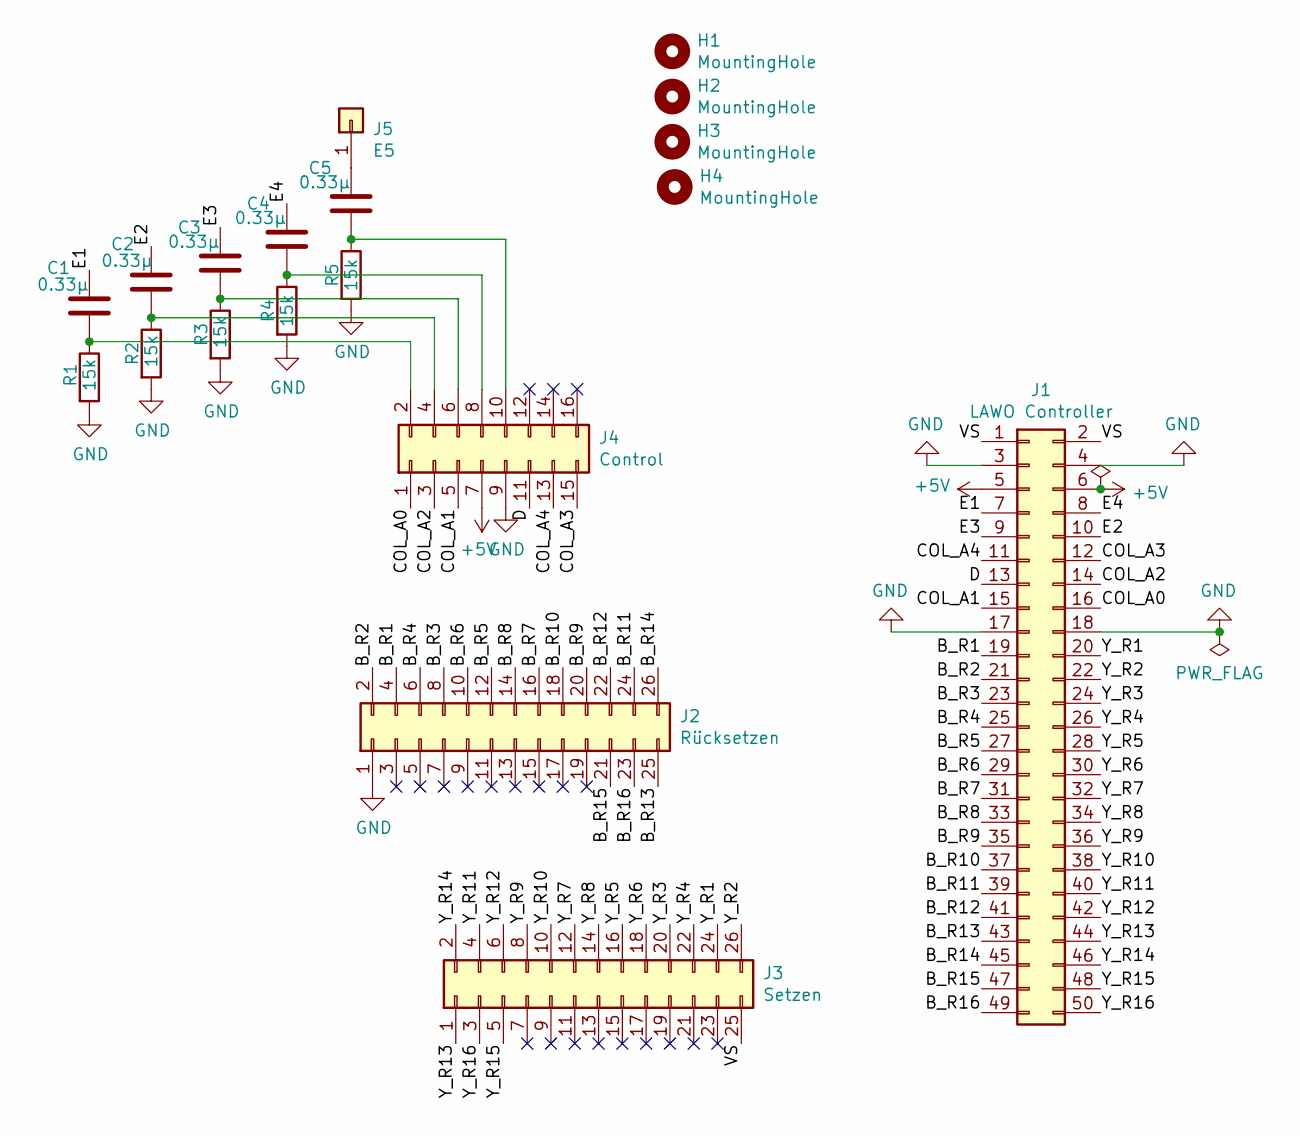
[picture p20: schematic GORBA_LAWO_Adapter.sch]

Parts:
C1, C2, C3, C4, C5: 0.33µ; C_Rect_L10.0mm_W4.0mm_P7.50mm_MKS4
H1, H2, H3, H4: MountingHole; MountingHole_2.7mm_Pad
J1: LAWO Controller; IDC_Header_Straight_50pins
J2: Rücksetzen; IDC_Header_Straight_26pins
J3: Setzen; IDC_Header_Straight_26pins
J4: Control; IDC_Header_Straight_16pins
J5: E5; PinHeader_1x01_P1.00mm_Vertical
R1, R2, R3, R4, R5: 15k; R_Axial_DIN0207_L6.3mm_D2.5mm_P7.62mm_Horizontal

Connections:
+5V: J1.5, J1.6, J4.7
/B_R1: J1.19, J2.4
/B_R2: J1.21, J2.2
/B_R3: J1.23, J2.8
/B_R4: J1.25, J2.6
/B_R5: J1.27, J2.12
/B_R6: J1.29, J2.10
/B_R7: J1.31, J2.16
/B_R8: J1.33, J2.14
/B_R9: J1.35, J2.20
/B_R10: J1.37, J2.18
/B_R11: J1.39, J2.24
/B_R12: J1.41, J2.22
/B_R13: J1.43, J2.25
/B_R14: J1.45, J2.26
/B_R15: J1.47, J2.21
/B_R16: J1.49, J2.23
/COL_A0: J1.16, J4.1
/COL_A1: J1.15, J4.5
/COL_A2: J1.14, J4.3
/COL_A3: J1.12, J4.15
/COL_A4: J1.11, J4.13
/D: J1.13, J4.11
/E1: C1.1, J1.7
/E2: C2.1, J1.10
/E3: C3.1, J1.9
/E4: C4.1, J1.8
/VS: J1.1, J1.2, J3.25
/Y_R1: J1.20, J3.24
/Y_R2: J1.22, J3.26
/Y_R3: J1.24, J3.20
/Y_R4: J1.26, J3.22
/Y_R5: J1.28, J3.16
/Y_R6: J1.30, J3.18
/Y_R7: J1.32, J3.12
/Y_R8: J1.34, J3.14
/Y_R9: J1.36, J3.8
/Y_R10: J1.38, J3.10
/Y_R11: J1.40, J3.4
/Y_R12: J1.42, J3.6
/Y_R13: J1.44, J3.1
/Y_R14: J1.46, J3.2
/Y_R15: J1.48, J3.5
/Y_R16: J1.50, J3.3
GND: J1.3, J1.4, J1.17, J1.18, J2.1, J4.9, R1.2, R2.2, R3.2, R4.2, R5.2
unnamed: C1.2, J4.2, R1.1
unnamed: C2.2, J4.4, R2.1
unnamed: C3.2, J4.6, R3.1
unnamed: C4.2, J4.8, R4.1
unnamed: C5.1, J5.1
unnamed: C5.2, J4.10, R5.1

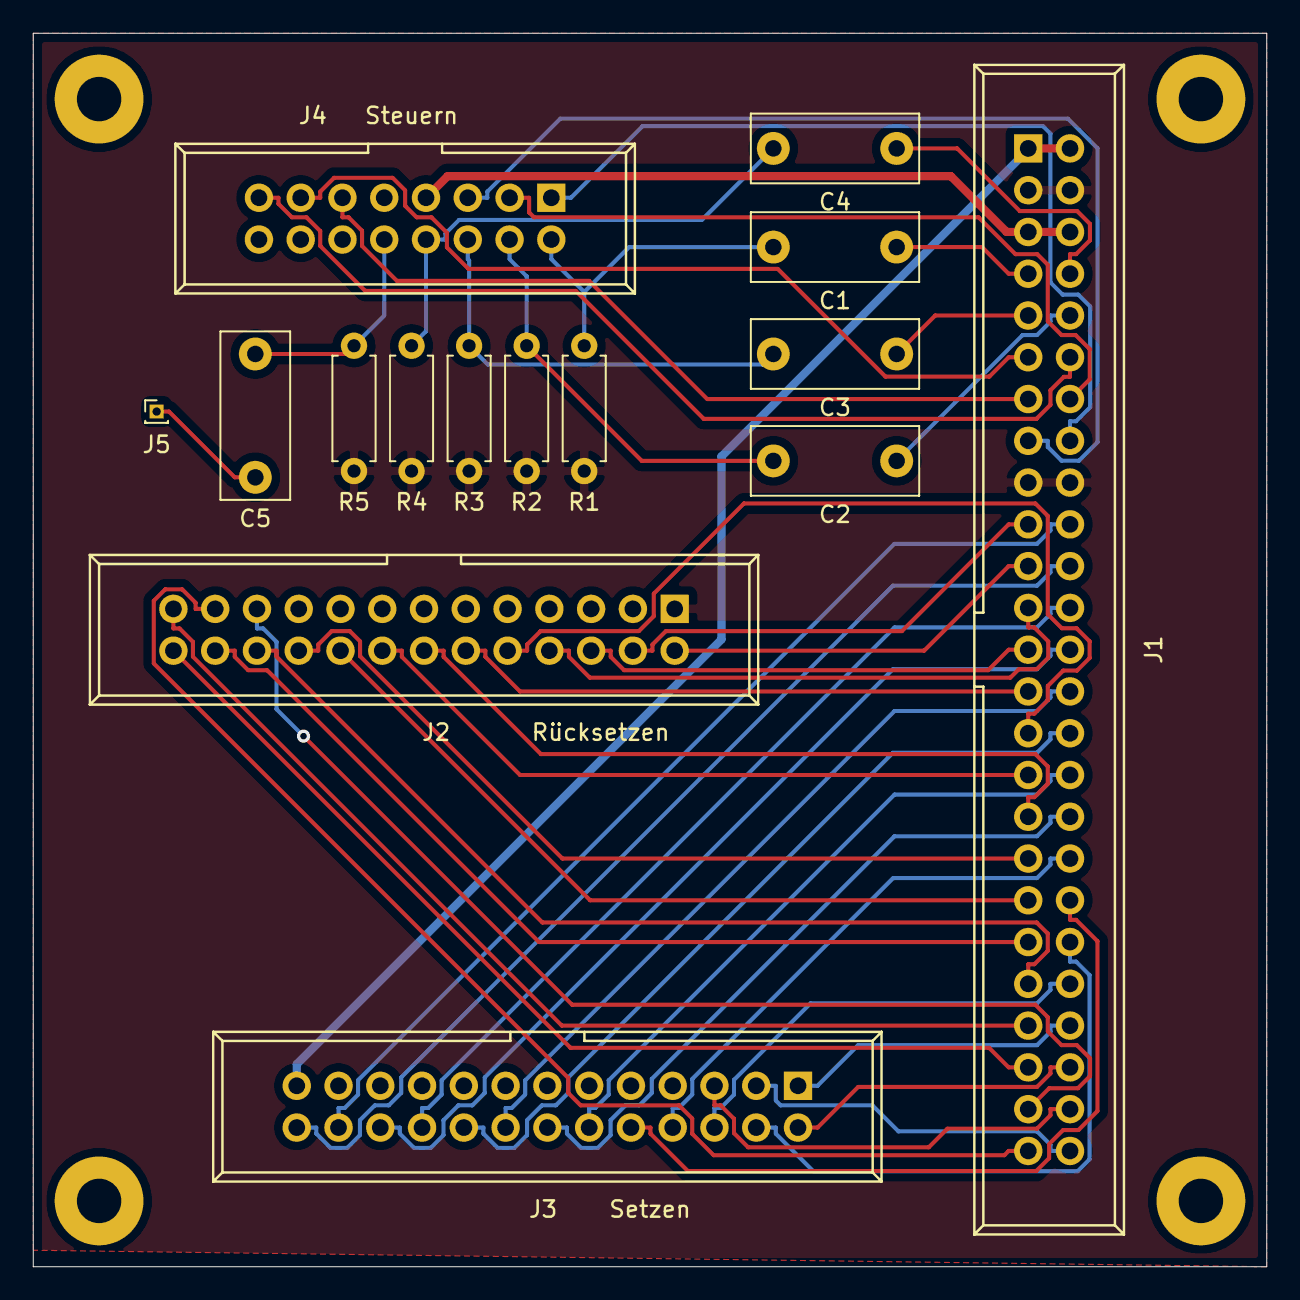
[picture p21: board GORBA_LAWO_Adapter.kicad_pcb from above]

Board: 2 copper layers, 75.0 x 75.0 mm, 19 parts (0 on the bottom side), 51 nets.

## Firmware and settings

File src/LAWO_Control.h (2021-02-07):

/*
 * LAWO_Control.h
 *
 *  Created on: 21 Apr 2020
 *      Author: pechj
 */

// Copyright (C) 2016 Julian Metzler
// modified in 2020 by Jérôme Pech

/*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
You should have received a copy of the GNU Affero General Public License
along with this program.  If not, see <http://www.gnu.org/licenses/>.
*/


#ifndef LAWO_CONTROL_H_
#define LAWO_CONTROL_H_

#include "LAWO_MCP23017.h"

#include "Icons.h"
#include "Font.h"

#define ADDRESS_ROW_MCP_Y     0x20
#define ADDRESS_ROW_MCP_B     0x21
#define ADDR_ROW_MCP_BROSE    0x23

#define FLIP_DURATION       2 // in microseconds
#define FLIP_PAUSE_DURATION 1 // in microseconds

#ifndef VIRTUAL_WIDTH
#define VIRTUAL_WIDTH (MATRIX_WIDTH*1)
#endif

enum pxStates {
  BLACK  = 0,
  YELLOW = 1
};

enum flipspeed {
  FS_NORMAL = 250,
  FS_SLOW   = 500
};

#ifndef _swap_int16_t
#define _swap_int16_t(a, b)                                                    \
  {                                                                            \
    int16_t t = a;                                                             \
    a = b;                                                                     \
    b = t;                                                                     \
  }
#endif

template<const uint8_t * COLUMN_LINES,const uint8_t * E_LINES, const uint8_t NUM_E_LINE_PINS, const uint8_t D, const uint8_t MCP_RESET = 0, const uint8_t LED = 0>
class LAWODisplay {
private:
  LawoFont lawoFont;
  MCP23017Type<ADDRESS_ROW_MCP_Y> ROW_MCP_Y;
  MCP23017Type<ADDRESS_ROW_MCP_B> ROW_MCP_B;
#ifdef USE_BROSE
  MCP23017Type<ADDR_ROW_MCP_BROSE> ROW_MCP_BROSE;
#endif
  uint16_t flipSpeedFactor;
  uint8_t lastColIndex;
  uint8_t lastRowIndex;
  uint8_t lastState;
  uint8_t charSpacing;
  bool initOK;
  bool mcp_ok;
  uint32_t PixelState[VIRTUAL_WIDTH];     //uint32_t 32bit represent up to 32 rows
  uint32_t NextPixelState[VIRTUAL_WIDTH]; //uint32_t 32bit represent up to 32 rows
private:
  void initPins() {
    if (MCP_RESET != 0)
      pinMode(MCP_RESET, OUTPUT);
    
    for (uint8_t i = 0; i < 5; i++) {
      pinMode(COLUMN_LINES[i], OUTPUT);
    }
    
    for (uint8_t i = 0; i< NUM_E_LINE_PINS; i++) {
      pinMode(E_LINES[i], OUTPUT);
    }    
    
    pinMode(D, OUTPUT);
    
    if (LED != 0)
      pinMode(LED, OUTPUT);
  }

  bool initMCP() {
    if (MCP_RESET != 0) {
      //strobe RESET to reset the chip
      digitalWrite(MCP_RESET, LOW);
      delay(2);
      digitalWrite(MCP_RESET, HIGH);
      delay(25);
    }
    //this initializes the MCP, sets all pins to OUTPUT and puts state LOW
    bool mcp_y_ok = ROW_MCP_Y.init();
    bool mcp_b_ok = ROW_MCP_B.init();
    mcp_ok = (mcp_y_ok && mcp_b_ok) ;

#ifdef USE_BROSE
    bool mcp_brose_ok = ROW_MCP_BROSE.init();
    mcp_ok = (mcp_ok && mcp_brose_ok);
#endif

    if (!mcp_ok) {
      Serial.println("Error while initializing MCP23017");
      return false;
    }
    return true;
  }

  void selectColumn(byte colIndex) {
    /*
     * Select the appropriate panel for the specified column index and set the column address pins accordingly.
     */
    if (initOK) {

#ifdef COL_SWAP
      colIndex = PANEL_WIDTH - colIndex - 1;
#endif

      // In the case of a matrix with a 14-col panel at the end instead of a 28-col one, we need to remember that our panel index is off by half a panel, so flip the MSB
      bool halfPanelOffset = hasHalfPanelOffset(colIndex);


      // Additionally, the address needs to be reversed because of how the panels are connected
      colIndex = MATRIX_WIDTH - colIndex - 1;

      // Since addresses start from the beginning in every panel, we need to wrap around after reaching the end of a panel
      byte address = colIndex % PANEL_WIDTH;

      // A quirk of the FP2800 chip used to drive the columns is that addresses divisible by 8 are not used, so we need to skip those
      address += (address / 7) + 1;

      digitalWrite(COLUMN_LINES[0], address & 1);
      digitalWrite(COLUMN_LINES[1], address & 2);
      digitalWrite(COLUMN_LINES[2], address & 4);
      digitalWrite(COLUMN_LINES[3], address & 8);
      digitalWrite(COLUMN_LINES[4], halfPanelOffset ? !(address & 16) : address & 16);

    }
  }

  void selectRow(byte rowIndex, bool yellow) {
    if (initOK && rowIndex < MATRIX_HEIGHT) {
#ifdef ROW_SWAP
      rowIndex = MATRIX_HEIGHT - rowIndex - 1;
#endif
      ROW_MCP_Y.writeAll(0);
      ROW_MCP_B.writeAll(0);
#ifdef USE_BROSE
      ROW_MCP_BROSE.writeAll(0);
#endif
      if (rowIndex < 16) {
        if (yellow)
          ROW_MCP_Y.writePin(rowIndex, HIGH);
        else
          ROW_MCP_B.writePin(rowIndex, HIGH);
      }
#ifdef USE_BROSE
      else {
         uint8_t pin = rowIndex - 16;
         ROW_MCP_BROSE.writePin(yellow ? pin + 8 : pin , HIGH);
      }
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

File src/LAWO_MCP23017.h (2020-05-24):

/*
 * LAWO_MCP23017.h
 *
 *  Created on: 26 Apr 2020
 *      Author: jp112sdl
 */

#ifndef LAWO_MCP23017_H_
#define LAWO_MCP23017_H_
#include <Arduino.h>

#define MCP23017_IODIRA 0x00
#define MCP23017_IODIRB 0x01
#define MCP23017_GPIOA  0x12
#define MCP23017_GPIOB  0x13
#define MCP23017_OLATA  0x14
#define MCP23017_OLATB  0x15

#include <Wire.h>

template <uint8_t MCP23017_ADDRESS=0x20>
class MCP23017Type {
private:
  bool    available        = false;
  uint8_t currentRegA      = 0x00;
  uint8_t currentRegB      = 0x00;

  bool initWire(uint8_t addr) {
    Wire.beginTransmission(addr);
    return (Wire.endTransmission() == 0);
  }

  uint8_t regForPin(uint8_t pin, uint8_t portAaddr, uint8_t portBaddr){
    return (pin<8) ? portAaddr : portBaddr;
  }

  uint8_t readRegister(uint8_t addr){
    Wire.beginTransmission(MCP23017_ADDRESS);
    Wire.write(addr);
    Wire.endTransmission();
    Wire.requestFrom((uint8_t)MCP23017_ADDRESS, (uint8_t)1);
    return Wire.read();
  }

  void updateRegisterBit(uint8_t pin, uint8_t pValue, uint8_t portAaddr, uint8_t portBaddr) {
    uint8_t regAddr=regForPin(pin,portAaddr,portBaddr);
    uint8_t bit=pin%8;
    uint8_t regValue = readRegister(regAddr);
    bitWrite(regValue,bit,pValue);
    writeRegister(regAddr,regValue);
  }

  void writeRegister(uint8_t regAddr, uint8_t regValue){
    Wire.beginTransmission(MCP23017_ADDRESS);
    Wire.write(regAddr);
    Wire.write(regValue);

    if (regAddr == MCP23017_OLATA)
      currentRegA = regValue;
    else if (regAddr == MCP23017_OLATB)
      currentRegB = regValue;

    Wire.endTransmission();
  }

  void pinMode(uint8_t p, uint8_t d) {
    updateRegisterBit(p,(d==INPUT),MCP23017_IODIRA,MCP23017_IODIRB);
  }

public:

  void writePin(uint8_t pin, uint8_t d) {
    uint8_t bit=pin%8;
    uint8_t regAddr=regForPin(pin,MCP23017_OLATA,MCP23017_OLATB);
    //uint8_t gpio = readRegister(regAddr);
    uint8_t gpio = regAddr == MCP23017_OLATA ? currentRegA : currentRegB;
    bitWrite(gpio,bit,d);
    regAddr=regForPin(pin,MCP23017_GPIOA,MCP23017_GPIOB);
    writeRegister(regAddr,gpio);
  }

  void writeAll(uint16_t ba) {
    Wire.beginTransmission(MCP23017_ADDRESS);
    Wire.write(MCP23017_GPIOA);
    Wire.write(ba & 0xFF);
    Wire.write(ba >> 8);
    Wire.endTransmission();
    currentRegA = ba & 0xFF;
    currentRegB = ba >> 8;
  }

  bool init() {
    Wire.begin();
    if (initWire(MCP23017_ADDRESS) == true) {
      writeRegister(MCP23017_IODIRA,0xff);
      writeRegister(MCP23017_IODIRB,0xff);
      for (uint8_t i = 0; i < 16; i++){
        pinMode(i, OUTPUT);
      }
      writeAll(0);
      available = true;
      Wire.setClock(800000L);
      return true;
    }
    Serial.printf("MCP23017Type: no MCP23017 found at address %#01x\n",MCP23017_ADDRESS);
    available = false;
    return false;
  }
};



#endif /* LAWO_MCP23017_H_ */

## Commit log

2020-05-24 speed up I2C Writes
2020-05-29 update BROSE_LAWO Adapter PCB
    [BROSE_LAWO_Adapter.kicad_pcb, BROSE_LAWO_Adapter.sch]
2020-06-15 add WEMOS_Adapter
    [WEMOS_Adapter-B_Cu.gbr, WEMOS_Adapter-B_Mask.gbr, WEMOS_Adapter-B_Paste.gbr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]
2020-07-04 update pcb
    [BROSE_LAWO_Adapter-B_Cu.gbr, BROSE_LAWO_Adapter-B_Mask.gbr, BROSE_LAWO_Adapter-B_Paste.gbr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]

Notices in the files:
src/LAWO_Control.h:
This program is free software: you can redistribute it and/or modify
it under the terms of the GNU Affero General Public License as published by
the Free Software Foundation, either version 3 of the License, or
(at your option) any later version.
